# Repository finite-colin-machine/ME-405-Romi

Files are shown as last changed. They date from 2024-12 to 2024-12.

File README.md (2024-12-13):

# ME-405-Romi
## Project Overview and Results
Romi
**Figure 1:** Finished robot

This is the repository for the Cal Poly ME-405 term project by Colin Bentley and Jack Maxwell that required building and programming a line following differential drive robot. The robot follows a black line from the start box to the finish box and navigates around a wall obstacle along the way. After finishing, the robot drives back to start and prepares for another run. The robot features a line sensor, bump sensors, and a 9-DOF absolute orientation IMU to read heading and yaw. The robot can successfully navigate the course. The line following is accurate, even with challenging shapes like dashes and horizontal lines in the path, and the control system results in smooth driving.

[Watch Romi complete the course](https://cpslo-my.sharepoint.com/:v:/g/personal/cobentle_calpoly_edu/EcgrodB_KnZJpqk-TpCn7YkBvjt-W66TGioHFDayowuLnw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)

This project has room for future improvements. Currently, the wall navigation parameters have to be preprogrammed. Having the robot slowly bump around the wall similar to a Roomba could make this program more flexible for unknown obstacles while keeping the same bump sensors. The navigation from start to finish relies on the start box being directly behind the robot when it finishes the course. Adding calculations for the robot's postion while running through the course would allow it to drive back to start even if the start and finish boxes were moved. The program could run faster by using an analog line sensor or by configuring the digital sensor to work with interupts to prevent the program from waiting while reading the line. We noticed that battery voltage has a noticable impact on performance, and the control gains should be tuned to the specific voltage for best results.

## Hardware
The robot is built off a Romi chassis and controlled using a Nucleo L476RG running MicroPython. An additional circuit board called the Shoe of Brian attaches to the Nucleo. Information about the shoe and general support for the techniques used in this project can be found [here](https://github.com/spluttflob/ME405-Support).

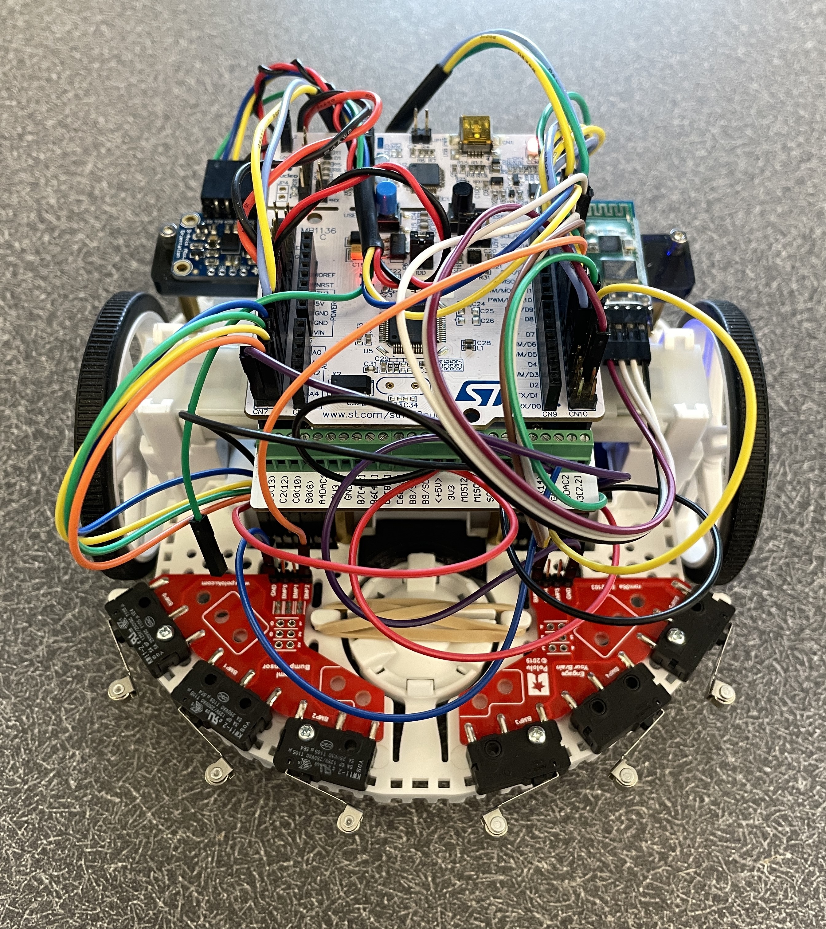
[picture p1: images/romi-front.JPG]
Romi Front


**Figure 2:** Romi front view with IMU and bluetooth module shown on the sides

The Nucleo attaches to standoffs and an acrylic mount as shown in this [model](https://cad.onshape.com/documents/b78783ff999bc8e6a9990234). The IMU and optional Bluetooth module are taped to the sides of the acrylic mount. The bump sensors screw directly to the front of the chassis, and the line sensor is taped to the line sensor mount which taped to the chassis.

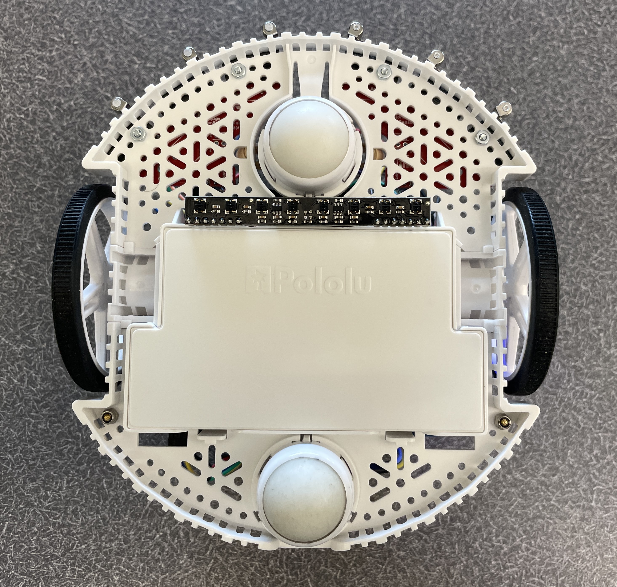
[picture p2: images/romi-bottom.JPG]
Romi Bottom


**Figure 3:** Romi bottom view with line sensor

Table 1 lists all of the parts besides the jumper wires used in this project.

**Table 1:** Complete BOM
| Part | Supplier  | P/N | Additional Info |
|---|---|---|---|
| Microcontroller | Nucleo | L476RG | |
| Shoe of Brian | Custom | N/A | [OSH Park](https://oshpark.com/shared_projects/e6X6OnYK) |
| Romi Chassis Kit | Pololu | 3509 | |
| Motor Driver and Power Distribution Board | Pololu | 3543 | |
| Line Sensor | Pololu | 3672 | |
| Right Bumper | Pololu | 3674 | |
| Left Bumper | Pololu | 3673 | |
| IMU | Adafruit  | 2472 | |
| Bluetooth Module | | HC-05  | Optional |
| Line Sensor Mount | Custom | N/A | See line-sensor-mount.STEP |
| Misc. mounts and fasteners | N/A | N/A | [Onshape](https://cad.onshape.com/documents/b78783ff999bc8e6a9990234) |

Figure 4 is a wiring diagram for the robot and, Table 2 lists the wire connections used.

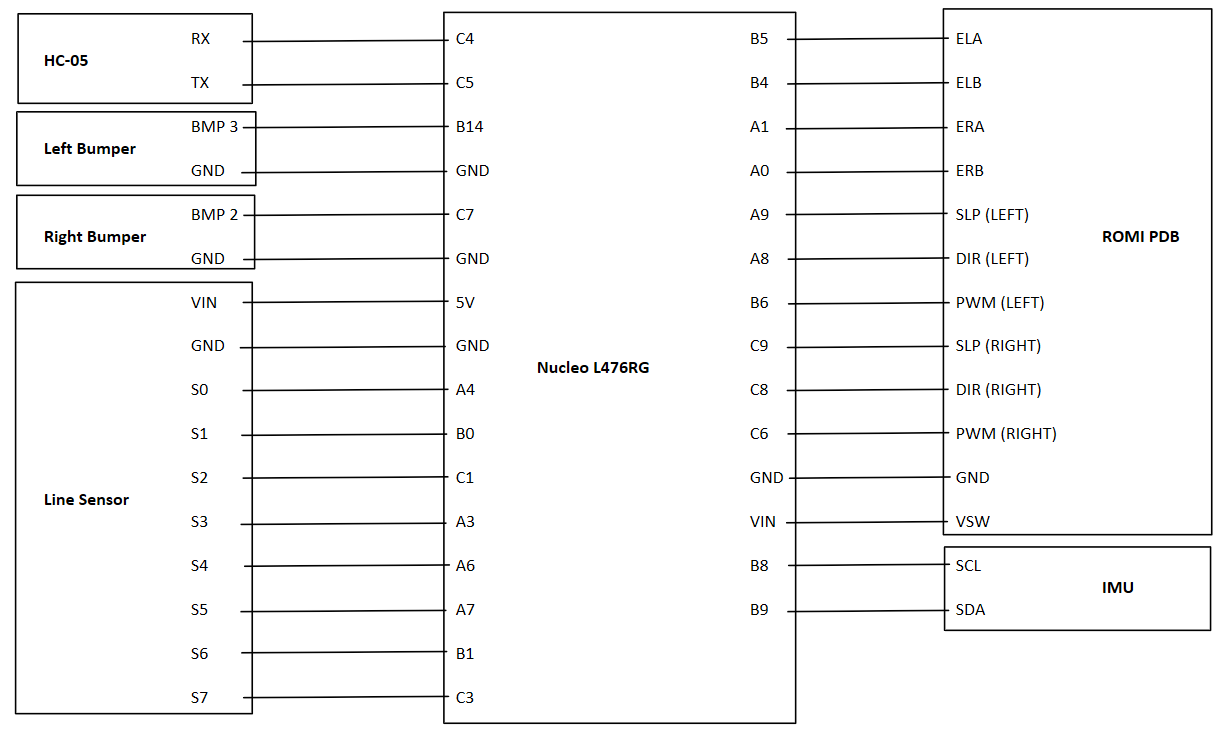
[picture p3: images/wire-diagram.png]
Wiring Diagram


**Figure 4:** Wiring diagram

**Table 2:** Wire connections
| Device/Function | Signal | Nucleo Pin | Device Pin |
|---|---|---|---|
| Left Encoder (Romi PDB)  | Enc Ch A | B5 (Tim 3) | ELA |
| | Enc Ch B | B4 (Tim 3) | ELB |
| Right Encoder (Romi PDB) | Enc Ch A | A1 (Tim 2) | ERA |
| | Enc Ch B | A0 (Tim 2) | ERB |
| Left Motor (Romi PDB) | Enable | A9 | SLP |
| | Direction | A8 | DIR |
| | Effort | B6 (Tim 4) | PWM |
| Right Motor (Romi PDB) | Enable | C9 | SLP |
| | Direction | C8 | DIR |
| | Effort | C6 (Tim 8) | PWM |
| Power (Romi PDB) | Ground | GND | GND |
| | Power | VIN | VSW |
| I2C | SCL | B8 | SCL |
| | SDA | B9 | SDA |
| HC-05 Bluetooth | RX | C4 | RX |
| | TX | C5 | TX |
| Left Bumper | BMP | B14 | BMP 3 |
| | GND | GND | GND |
| Right Bumper | BMP | C7 | BMP 2 |
| | GND | GND | GND |
| Line Sensor | Power | 5V | VIN |
| | GND | GND | GND |
| | Sensor 0 | A4 | S0 (R) |
| | Sensor 1 | B0 | S1 |
| | Sensor 2 | C1 | S2 |
| | Sensor 3 | A3 | S3 |
| | Sensor 4 | A6 | S4 |
| | Sensor 5 | A7 | S5 |
| | Sensor 6 | B1 | S6 |
| | Sensor 7 | C3 | S7 (L) |

Additionally, the IMU and Bluetooth Module are both wired to +5V and GND for their power supply.

## Code
The code folder contains all of the files that need to be stored on the Nucleo in order to run. This project uses MicroPython, which the nucleo needs to be preconfigured with before adding the other files. [main.py](code/main.py) contains the code to create and run the task structure, along with the initialization for all of the devices connected to the microcontroller. [encoder.py](code/encoder.py), [Romi_Motor.py](code/Romi_Motor.py), [BNO055.py](code/BNO055.py), and [line_sensor.py](code/line_sensor.py) contain classes for interacting with the encoders, motors, IMU, and line sensor repsectivly.

### Task Structure
Figure 5 contains the overall task diagram for the program that is run using preemptive multitasking. Scheduling and shares are handled by [cotask.py](code/cotask.py) and [task_share.py](code/task_share.py). We tuned the tasks to run as frequently as possible while still allowing all of the other tasks to run. The Planner has the highest priority but does not need to run often. Driving Mode has the next highest priority and needs to run often enough to get good line measurements; however, the line reading is time intensive and can easily overpower the other tasks if the period is too low. The control tasks have the lowest priority and run most often. This we can consistently measure good data and adjust the control setpoints, but it is okay if a higher priority task briefly blocks the control tasks from running.

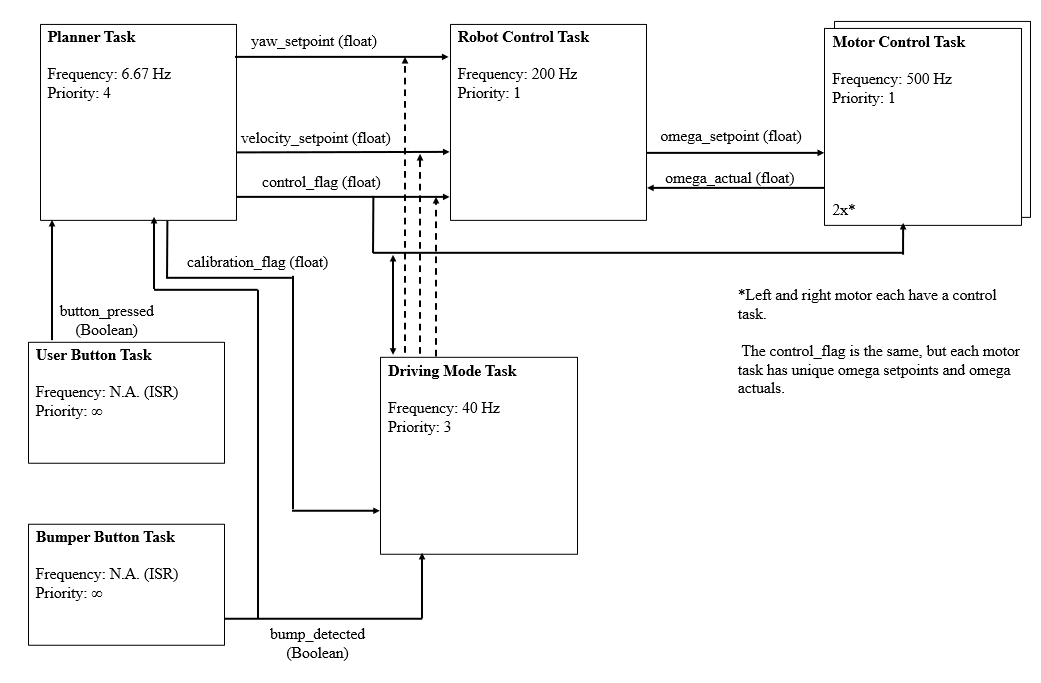
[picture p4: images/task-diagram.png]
Task Diagram


**Figure 5:** Overall task diagram

The Planner Task in our code is less complex than the other tasks, but is still crucial to the success of the program. In State 0, some system parameters are initialized, and on startup and when the code is reset from the PuTTY REPL, the task switches to State 2 for calibration. Upon successful calibration the task moves to State 1, where you are prompted to press the blue button to begin driving. Pressing the blue button will enable the system control loop and allow the robot to begin moving forward.

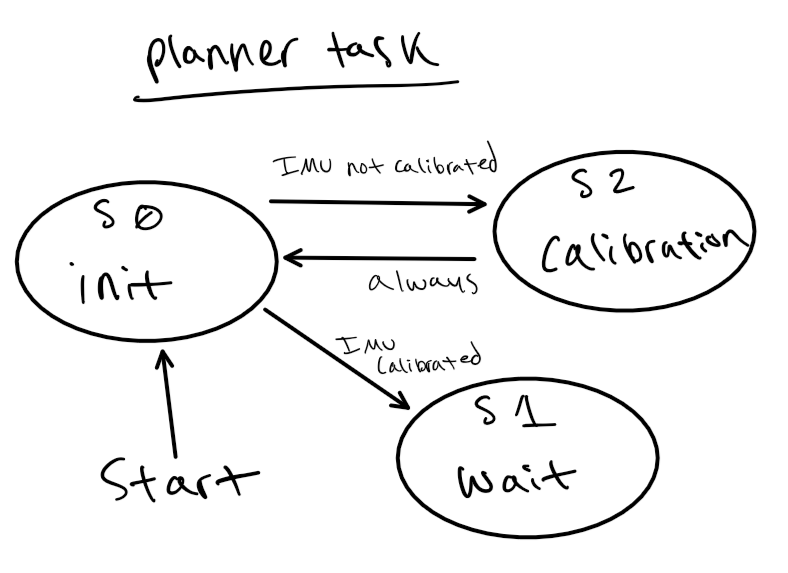
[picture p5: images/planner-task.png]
Planner Task


**Figure 6:** Planner Task State Transition Diagram

The robot control task is the outer loop of our system control, as seen in Figure 7. In State 1, this task takes in the translational velocity and yaw rate setpoints calculated by the driving mode task, as well as the actual wheel velocities calculated by the motor control task. Using the individual wheel velocities, this task calculates the actual translational velocity, and using the heading data from the IMU, calculates the actual yaw rate of Romi. PI Control (proportional and integral control) is performed on these values to calculate a velocity request and a yaw rate request, which are converted to a left and right wheel speed request, which are then sent to the individual wheel control tasks using shares. In State 0, the timer used to calculate the integral error for integral control is continuously reset to avoid integral error buildup while the control is off.

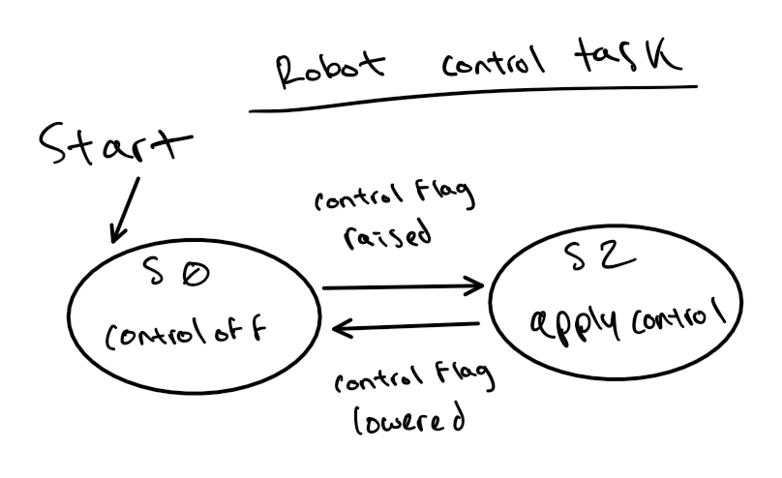
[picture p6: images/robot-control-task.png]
Robot Control Task


**Figure 7:** Robot Control Task State Transition Diagram

The motor control tasks act similarly to the overall robot control. They take in the setpoints for wheel velocity calculated by robot control and perform PI control on them to determine the duty cycle percentage that is sent to each motor. The actual velocities are sent to the robot control task when they are measured. Like the robot control, State 0 updates the encoder each pass-through to avoid integral error buildup.

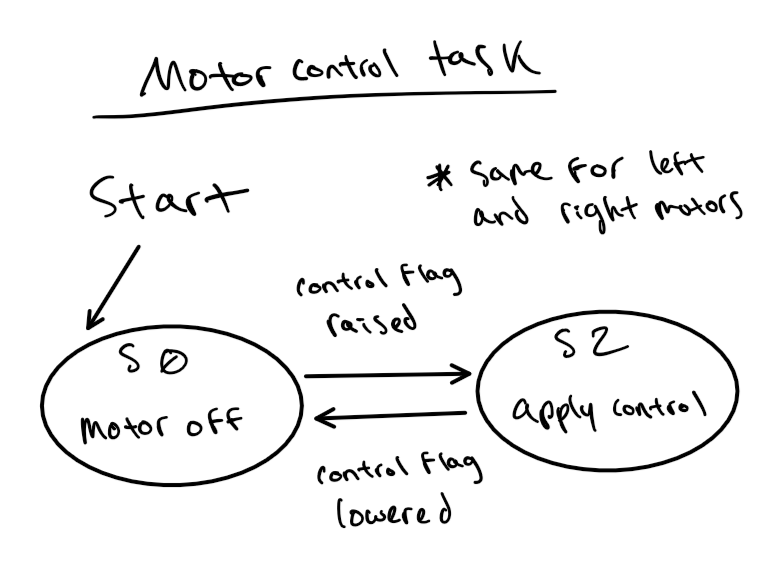
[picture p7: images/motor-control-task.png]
Motor Control Task


**Figure 8:** Motor Control Task State Transition Diagram

The driving mode task is our most complex task, as it is responsible for keeping the robot on the line and making it drive around the obstacle on the course. State 0 initializes some variables and flagsthat are used throughout the task, and when the system control flag is raised by the planner task, it moves to State 3, which instructs it to drive forward to leave the starting area. Once the robot has left the starting area, State 1 is entered, which is our main line-following state. This state reads the line sensor, and sends a yaw rate request to the system control based on the location of the line relative to the robot. When a bump is detected by the bump sensors mounted to the robot, the task enters State 2, where the robot is given a specific set of instructions to drive around the obstacle on the course, before returning to State 1 for line following.

When the robot enters the finishing area, the task enters State 4, where the robot drives to the center of the finishing area, and turns in place until its heading is 180 degrees past that of its initial heading. It then begins driving straight backwards and enters State 5. In State 5, the robot drives straight backward until it detects the starting area, where the task then enters State 6 to center itself in the box, and finally enters State 7 to turn the robot around and re-initialize the program to prepare for future runs.

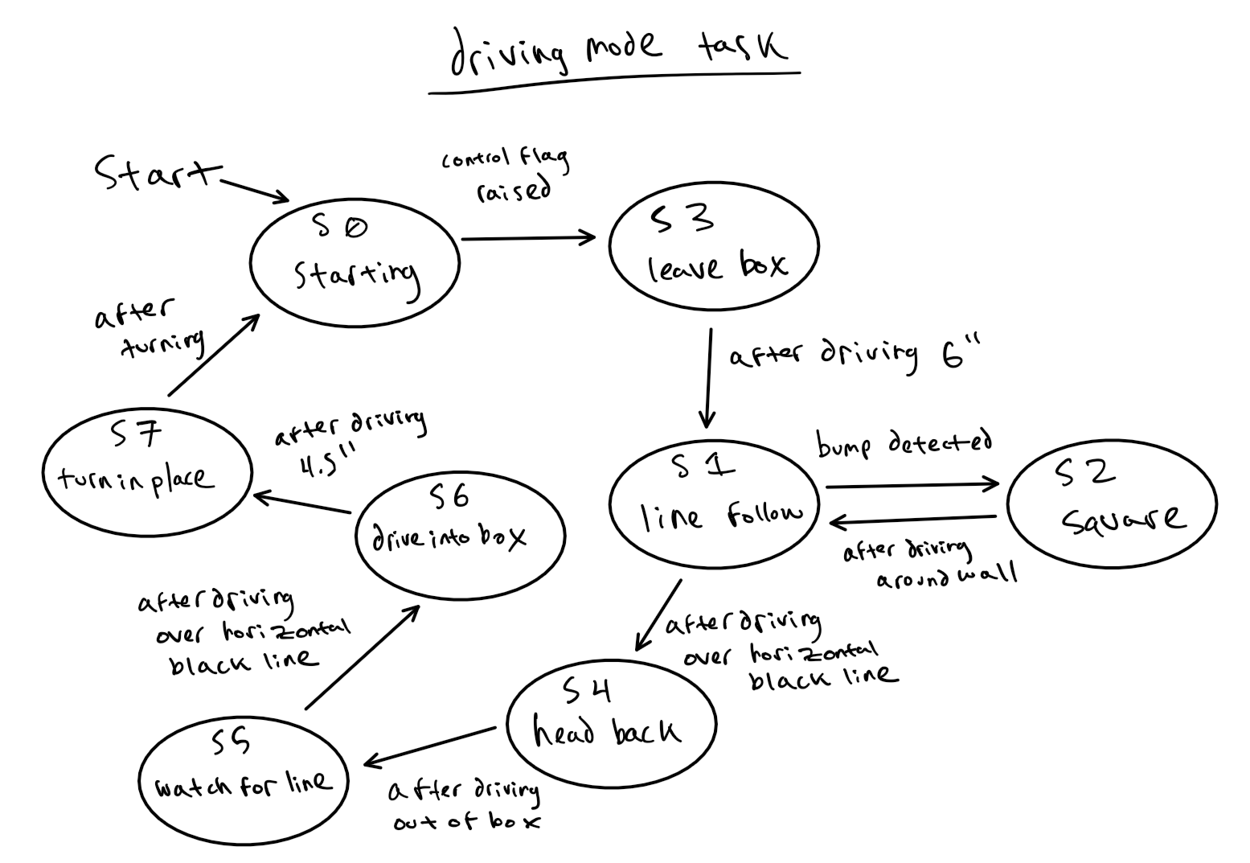
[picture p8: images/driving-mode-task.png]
Driving Mode Task


**Figure 9:** Driving Mode Task State Transition Diagram

### Control System
Figure 5 depicts the overall control system for the robot. We specify velocity and setpoints for the robot control loop either manually or using feedback from devices like the line sensor. . The robot control calculates the actual translational velocity using wheel speed measurements from the motor tasks and gathers yaw measurements from the IMU. Both are fed through PI control to become velocity and yaw requests. Omega setpoints are calculated from these requests using the robot parameters and sent to each of the motor control tasks. The motor control tasks perform PI control of the left and right wheel speeds using omega setpoints from the robot control and real omega measurements calculated from the encoders.

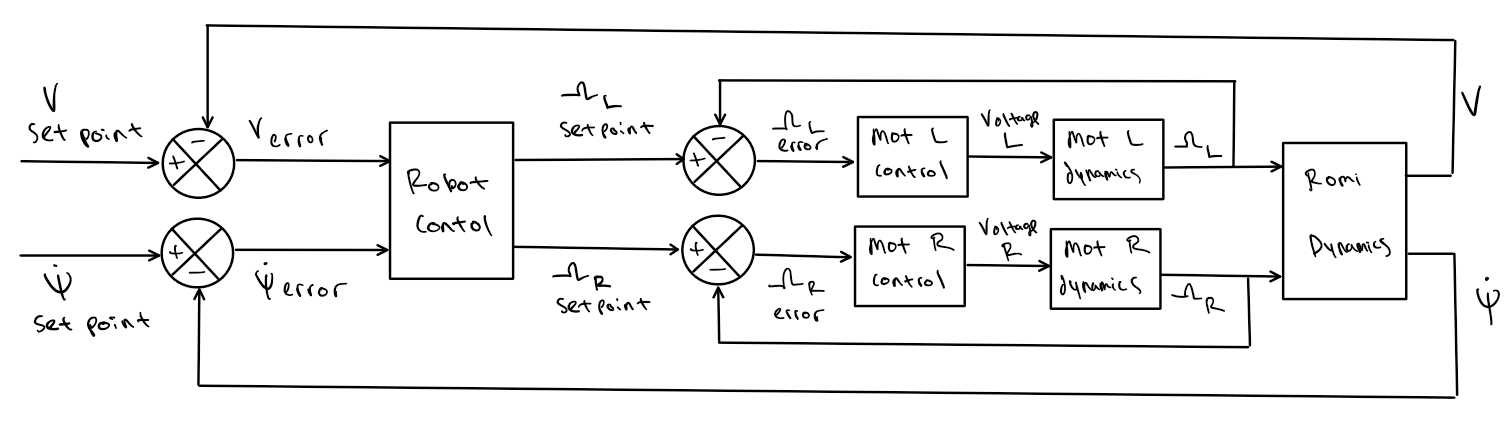
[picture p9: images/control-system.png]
Control System


**Figure 10:** Overall control system

## Supporting Calculations
Figures 11 and 12 show the calculations for translational velocity from the wheel speeds and the angular velocity setpoints from the velocity and yaw setpoints. These calculations are performed in the robot control task.

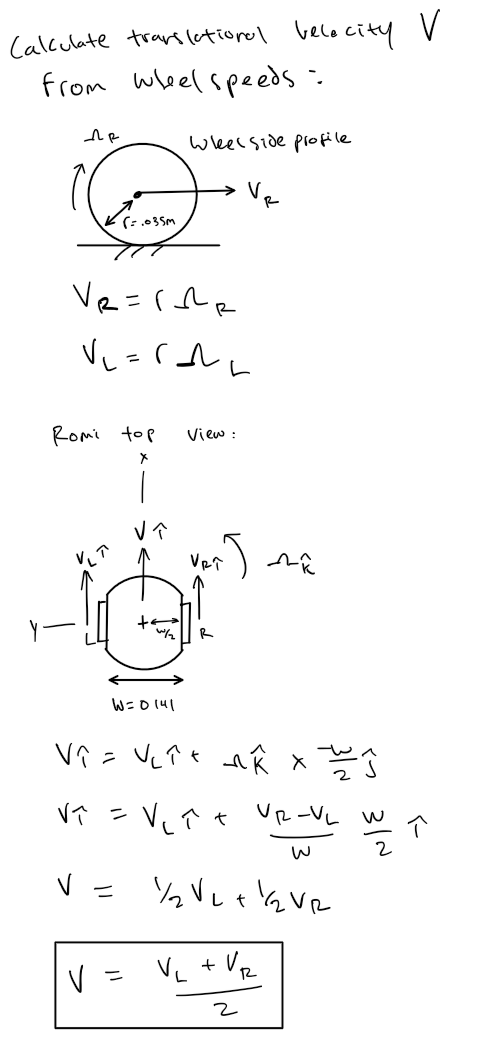
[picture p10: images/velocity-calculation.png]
Translational Velocity Calculation


**Figure 11:** Translational velocity calculation

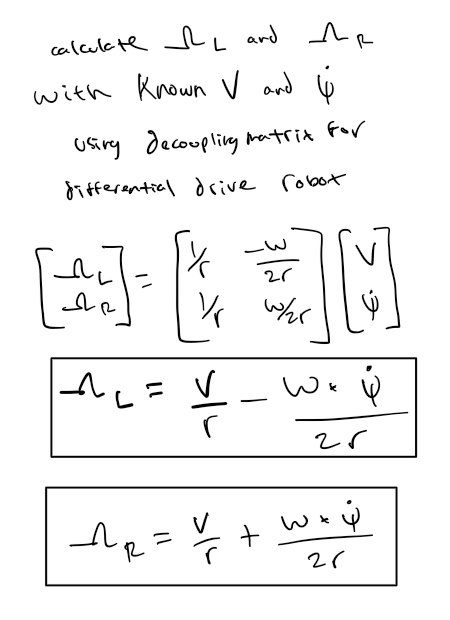
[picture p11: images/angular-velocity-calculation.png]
Angular Velocity Calculation


**Figure 12:** Angular velocity calculation

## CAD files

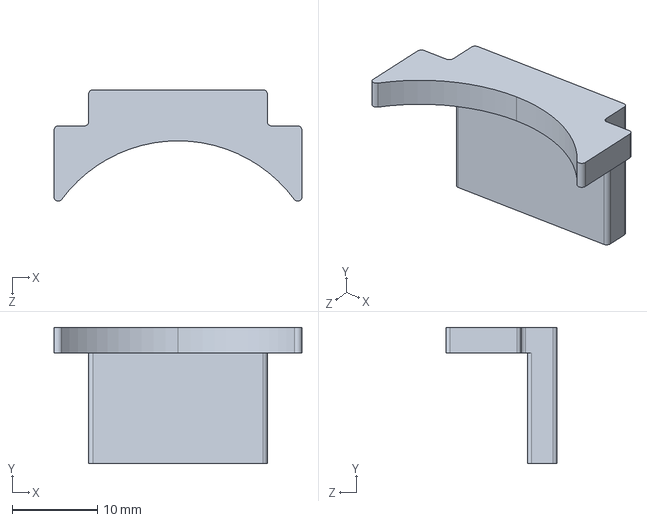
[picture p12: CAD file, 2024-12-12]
line-sensor-mount.STEP
29.2 x 16.0 x 13.1 mm

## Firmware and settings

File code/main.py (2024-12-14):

"""!
@file main.py 
@author Colin Bentley and Jack Maxwell
@date 12/13/2024

This program is used to make a Romi robot follow a line-based obstacle course.
This program is part of assignment Term Project 0x02 - Romi Time-Trials for ME 405.

Users place Romi inside the starting area and press the blue botton to start, and
thr robot autonomously guides itself through the course to the finsih line, and returns
to the startimng area.

Romi accomplishes this by taking readings with a line sensor, which are converted to 
yaw-rate changes for the control scheme to follow. Additionally, there is a bump sensor
mounted to the robot that when presses, puts the robot into a pre-set path around the 
obstacle before resuming line-following.

The standard control scheme uses a robot control task that takes in yaw rate and velocity
information, and feeds wheel speed setpoints to the motor control tasks.
"""

# Import modules
from pyb import Pin, Timer, UART, repl_uart, ExtInt
import gc
import machine
import cotask
import task_share
from encoder import encoder
from Romi_Motor import Romi_Motor             
from BNO055 import BNO055
from time import ticks_us, ticks_diff, sleep_ms
from math import pi
from line_sensor import line_sensor

# Blue user button function
def user_button_toggle(pressed):
    global user_button_pressed
    user_button_pressed = True

# Bump sensor function
def bump_toggle(pressed):
    global bump_detected
    bump_detected = True
    print('Hey! Who put that there?')
    # The bump sensors have a small amount of signal bouncing - this
    # is handled by not resetting the bump_detected flag until the
    # end of the pre-coded sequence.

# Create generator functions acting as tasks containing FSMs
def planner(shares):
    """!
    Task which handles the IMU calibratrion and waits for the blue button to be pressed.
    @param shares A tuple of a share and queue from which this task gets data
    """
    global user_button_pressed, bump_detected # list global variables
    
    # get references to the shares and queues which have been passed to this task
    my_velocity_setpoint, my_yaw_setpoint, my_control_flag, my_calibration_flag = shares
    
    state = 0                  # initialize state
    calibrated = False         # initialize calibration
    my_calibration_flag.put(0) # initialize calibration flag

    while True:
        if (state == 0):                        # init state
            V = .10                             # user input robot translational velocity [m/s]
            
            # # # TO BYPASS CALIBRATION CHECK
            # calibrated = True
            # print('bypassing calibration')
            
            if calibrated == False:
                state = 2   # set calibration state
            else:
                print('Press blue button to begin driving')
                state = 1   # set wait state
            yield(state)  
            
        elif (state == 1):  # wait and search for bump state state
            if user_button_pressed == True:
                user_button_pressed = False    # if so, reset the user button flag
                my_control_flag.put(1)         # raise control flag       
                my_velocity_setpoint.put(V)    # set velocity for robot control task
                my_yaw_setpoint.put(0)         # set yaw rate for robot control task
            yield(state)
        
        elif (state == 2):                           # calibration state
            
            file_known = False                       # initialize flag
            calibrated = False                       # initialize calibration status
        
            try:                                     # try to open calibration file
                with open('calibration.bin', 'r'):
                    file_known = True                # set flag
            except OSError:                          # if there is no calibration file
                print('Perform manual calibration')  # notify user
        
            if file_known:
                try:
                    IMU.set_offsets()                # calibrate using file data
                    calibrated = True                # set calibrated
                except OSError:                      # if there is an error using the file
                    raise OSError('''Error accessing calibration.bin. Remove calibration.bin from the nucleo and restart program to perform manual calibration''')
                                  
        
            if not calibrated:                       # if still not calibrated
                IMU.read_cal_status()                # read calibration status
                print(f"{IMU.mag_cal_status} {IMU.acc_cal_status} {IMU.gyr_cal_status} {IMU.sys_cal_status}")
                if (IMU.mag_cal_status == 3
                    and IMU.acc_cal_status == 3
                    and IMU.gyr_cal_status == 3
                    and IMU.sys_cal_status == 3):    # if all calibrated
                    calibrated = True                # set calibrated
                    print('IMU Calibrated')          # notify user
                    my_calibration_flag.put(1)
                    
            state = 0                                # set init state
            yield(state)
        
        else: # if state isnt found
            raise ValueError('Invalid state')

def robot_control(shares):
    """!
    Controller task which calculates omega setpoints for the motors using translationa velocity and yaw data.
    Comment out this task and follow other instructions in the code to bypass the robot control.
    @param shares A tuple of a share and queue from which this task gets data
    """
    global w, r # list global variables
    
    # get references to the shares and queues which have been passed to this task
    my_velocity_setpoint, my_yaw_setpoint, my_control_flag, my_omega_L_setpoint, my_omega_R_setpoint, my_omega_L_actual, my_omega_R_actual = shares
    
    V_err = 0       # zero error
    yaw_err = 0     # zero error
    V_err_sum = 0   # zero error sum
    yaw_err_sum = 0 # zero error sum
    
    state = 0       # initialize state
    
    # set proportional and integral gains for translational velocity and yaw rate
    Kp_V = .8
    Kp_yaw = .7
    Ki_V = .87
    Ki_yaw = .95
    
    while True:
        control_on = my_control_flag.get() # get control flag
        
        if state == 0:            # State 0: Robot Control off
            time_old = ticks_us() # continuously update old time while off
            if control_on == 0:   # set to control state if flag raised
                pass
            else:
                state = 1         # set control state
            yield(state)                   
            
        elif state == 1: # State 1: Apply control     

            # get values from shares
            V_ref = my_velocity_setpoint.get()
            yaw_ref = my_yaw_setpoint.get()
            omega_L_act = my_omega_L_actual.get()
            omega_R_act = my_omega_R_actual.get()
            
            # perform time calculations
            time_new = ticks_us()                         # update time
            dt = ticks_diff(time_new, time_old)/1_000_000 # calculate time difference in seconds
            time_old = time_new                           # reset the old time for next pass 
        
            # calculate actual translational velocity based on current wheel velocity
            V_act = (r/2)*(omega_L_act + omega_R_act)     
            
            # read actual yaw rate from IMU
            IMU.read_gyr()              
            yaw_act = IMU.gyr_z*0.01745 # [rad/s] convert yaw rate from deg/s to rad/s
      
            # calculate errors
            V_err = V_ref - V_act
            yaw_err = yaw_ref - yaw_act
            
            # calculate error sums
            V_err_sum += V_err*dt
            yaw_err_sum += yaw_err*dt
            
            # calculate robot requests by applying proportional and integral control
            V_request = Kp_V*V_err + Ki_V*V_err_sum
            yaw_request = Kp_yaw*yaw_err + Ki_yaw*yaw_err_sum
            
            # calculate wheel velocity requests from robot requests
            omega_L_request = (V_request/r) - (w*yaw_request/(2*r))
            omega_R_request = (V_request/r) + (w*yaw_request/(2*r))
            
            # add wheel velocities to shares
            my_omega_L_setpoint.put(omega_L_request)
            my_omega_R_setpoint.put(omega_R_request)
            
            if control_on == 1: # set to control off state if flag lowered
                pass
            else:
                V_err = 0       # zero velocity error
                yaw_err = 0     # zero yaw rate error
                V_err_sum = 0   # zero velocity error sum
                yaw_err_sum = 0 # zero yaw rate error sum

                state = 0       # set off state
            yield(state)
           
        else:                   # if state isnt found
            raise ValueError('Invalid state')

def motor_L_control(shares):
    """!
    Task which controls the velocity of the left motor by applying proportional and integral control to the velocity error
    @param shares is a tuple of a share and queue from which this task gets data
    """
    # get references to the shares and queues which have been passed to this task
    my_omega_L_setpoint, my_omega_L_actual, my_control_flag = shares
    
    state = 0       # initialize state
    mot_L.disable() # disable motor
    Kp = 7          # set proportional gain
    Ki = 8          # set integral gain
    err_sum = 0     # initialize error sum
    
    while True:
        motor_on = my_control_flag.get() # get control flag from shares
        
        if state == 0:        # State 0: Motor Off
        
            enc_L.update()    # continuously update encoder while off
            if motor_on == 0: # set to control state if flag raised
                pass
            else:
                mot_L.set_duty(0) # clear duty cycle
                mot_L.enable()    # enable motor
                state = 1         # set control state
            yield(state)
        
        elif state == 1: # State 1: Apply Motor Control
            
        # get wheel velocity from shares
            Omega_L_ref = my_omega_L_setpoint.get()
            
            # update encoder and get dt
            enc_L.update()
            dt = enc_L.get_dt()/1_000_000 # [s]
            
            # calculate omega actual
            Omega_act = enc_L.get_speed()*-4363 # [rad/s], multiplier is speed count/us * 10^6 us/s * 1/1440 rev/count * 2pi rad/rev
            my_omega_L_actual.put(Omega_act)    # add to wheel velocity share

            # Apply motor control
            err = Omega_L_ref - Omega_act # calculate error
            err_sum += err*dt             # calculate error sum
            L = Kp*err + Ki*err_sum       # calculate duty cycle
            mot_L.set_duty(L)             # set duty cycle
            
            if motor_on == 1:     # set to off state if flag lowered
                pass
            else:
                mot_L.set_duty(0) # clear duty cycle
                mot_L.disable()   # disable motor
                err_sum = 0       # clear error sum
                state = 0         # set off state
            yield(state)

def motor_R_control(shares):
    """!
    Task which controls the velocity of the right motor by applying proportional and integral control to the velocity error
    @param shares is a tuple of a share and queue from which this task gets data
    """
    # get references to the shares and queues which have been passed to this task
    my_omega_R_setpoint, my_omega_R_actual, my_control_flag = shares
    
    state = 0       # initialize state
    mot_R.disable() # disable motor
    Kp = 7          # set proportional gain
    Ki = 8          # set integral gain
    err_sum = 0     # initialize error sum
    
    while True:
        motor_on = my_control_flag.get() # get control flag from shares
        
        if state == 0:        # State 0: Motor Off
            
            enc_R.update()    # continuously update encoder while off
            if motor_on == 0: # set to control state if flag raised
                pass
            else:
                mot_R.set_duty(0) # clear duty cycle
                mot_R.enable()    # enable motor
                state = 1         # set control state
            yield(state)
        
        elif state == 1: # State 1: Apply Motor Control
            
            # get wheel velocity from shares
            Omega_R_ref = my_omega_R_setpoint.get()
            
            # update encoder and get dt
            enc_R.update()
            dt = enc_R.get_dt()/1_000_000 # [s]
            
            # calculate omega actual
            Omega_act = enc_R.get_speed()*-4363 # [rad/s], multiplier is speed count/us * 10^6 us/s * 1/1440 rev/count * 2pi rad/rev
            my_omega_R_actual.put(Omega_act)    # add to share

            # Apply motor control
            err = Omega_R_ref - Omega_act # calculate error
            err_sum += err*dt             # calculate error sum
            L = Kp*err + Ki*err_sum       # calculate duty cycle
            mot_R.set_duty(L)             # set duty cycle
            
            if motor_on == 1:     # set to off state if flag lowered
                pass
            else:
                mot_R.set_duty(0) # clear duty cycle
                mot_R.disable()   # disable motor
                err_sum = 0       # clear error sum
                state = 0         # set off state
            yield(state)
            
def driving_mode(shares):
    """!
    Task which handles the line following and obstacle avoidance behavior of the robot. The robot
    follows the line until a bump is detected, drives around the obstacle, and returns to line
    following until reaching the finish line, where the robot then returns to the start.
    @param shares is a tuple of a share and queue from which this task gets data 
    """
    global bump_detected # list global variables
    
    # get references to the shares and queues which have been passed to this task
    my_velocity_setpoint, my_yaw_setpoint, my_control_flag, my_calibration_flag = shares
    
    V = .10                             # user input robot translational velocity [m/s]
    w = .141                            # robot track width [m]
    r = .035                            # robot wheel radius [m]
    
    drive_3 = 1440*3*.0254/(2*pi*r)     # distance for robot to drive 3 inches [encoder counts]
    turn_90 = 1440*w/(8*r)              # distance for robot to turn 90 degrees in place [encoder counts]
    
    # init variables
    after_wall = False  # flag that is raised once the obstacle has been cleared
    state = 0
    
    while True:
        if state == 0:                                 # starting state
            control_on = my_control_flag.get()         # get control flag
            calibrated = my_calibration_flag.get()     # get calibration flag
            if calibrated == 0:                        # ignore bump detection before calibration
                bump_detected = False
            if control_on == 1:                        # set to control state if flag raised
                IMU.read_euler()                       # read the IMU
                starting_heading = IMU.euler_heading   # retrieve the robots heading to allow it to return to the start
                enc_R.zero()                           # clear encoder position
                state = 3                              # set leave box
            yield(state)                   
        
        elif state == 1:                                        # line follow state
            if bump_detected:                                   # if there is a bump
                my_control_flag.put(0)                          # turn off motors
                enc_R.zero()                                    # clear encoder
                section_complete = False                        # Initialize square section completion flag
                square_idx = 1                                  # Init square index
                state = 2                                       # set square driving state
            elif after_wall == True and qtr.full_black == True: # if robot crosses black line after bumping wall, it's at the finish line
                my_velocity_setpoint.put(V)                     # set velocity
                my_yaw_setpoint.put(0)                          # set yaw
                enc_R.zero()                                    # clear encoder
                after_wall = False                              # reset flag for future runs
                return_idx = 1                                  # initialize return sequence index
                state = 4                                       # set turn around state
            else:                                               # otherwise
                yaw = qtr.read_line()/1500                      # read line and scale measurement
                if qtr.full_black:                              # if the robot senses a prependicular line
                    my_yaw_setpoint.put(0)                      # set yaw to zero to minimize "twitching"
                else:
                    my_yaw_setpoint.put(yaw)                    # Set yaw based on line reading
            yield(state)   
            
        elif state == 2:                          # drive in square state
            enc_R.update()                        # Update encoder position
            position = abs(enc_R.get_position())  # Get position magnitude
            
            if square_idx == 1 and not section_complete:  # Step 1: Back up
                my_velocity_setpoint.put(-V)  # Set reverse velocity
                my_yaw_setpoint.put(0)        # No yaw change
                my_control_flag.put(1)        # Start movement
                if position > drive_3 / 2:    # Condition to finish backing up
                    my_control_flag.put(0)    # turn off control so the robot stops at each step
                    square_idx += 1           # increase the square path index
                    enc_R.zero()              # zero encoders
                    section_complete = True   # raise section complete flag so the next square step isn't entered immediately
            
            elif square_idx in [2, 4] and not section_complete:  # Steps 2 and 4: Turn 90 degrees
                turn_speed = -pi/2 if square_idx == 2 else pi/2  # turn left for state 2, right for state 4
                my_velocity_setpoint.put(0)      # No forward motion
                my_yaw_setpoint.put(turn_speed)  # Set yaw rate
                my_control_flag.put(1)           # Start turn
                if position > turn_90:           # Condition to finish turn
                    my_control_flag.put(0)
                    square_idx += 1
                    enc_R.zero()
                    section_complete = True
            
            elif square_idx == 3 and not section_complete:  # Steps 3: Drive forward short distance
                my_velocity_setpoint.put(V)  # Forward velocity
                my_yaw_setpoint.put(0)       # No yaw change
                my_control_flag.put(1)       # Start forward motion
                if position > drive_3 * 3:   # Condition to finish drive
                    my_control_flag.put(0)
                    square_idx += 1
                    enc_R.zero()
                    section_complete = True
            
            elif square_idx == 5 and not section_complete:  # Step 5: Drive forward longer distance
                my_velocity_setpoint.put(V)  # Forward velocity
                my_yaw_setpoint.put(0)       # No yaw change
                my_control_flag.put(1)       # Start forward motion
                if position > drive_3 * 6:   # Condition to finish drive
                    my_control_flag.put(0)
                    square_idx += 1
                    enc_R.zero()
                    section_complete = True
                    
            elif square_idx == 6 and not section_complete:  # Step 6: Turn slightly less than 90 degrees
                my_velocity_setpoint.put(0)  # No forward motion
                my_yaw_setpoint.put(pi/2)    # Set yaw rate
                my_control_flag.put(1)       # Start turn
                if position > turn_90 * .65: # Condition to finish turn
                    my_control_flag.put(0)
                    square_idx += 1
                    enc_R.zero()
                    section_complete = True
                    
            elif square_idx == 7 and not section_complete:  # Step 7: Drive forward until the line has been reached
                my_velocity_setpoint.put(V)  # Forward velocity
                my_yaw_setpoint.put(0)       # No yaw change
                my_control_flag.put(1)       # Start forward motion
                if position > drive_3 * 4:   # Condition to finish drive
                    enc_R.zero()
                    square_idx = 0          # Reset for future operations
                    bump_detected = False   # reset the bump detection flag
                    after_wall = True       # raise obstacle cleared flag
                    state = 1               # return to line following
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

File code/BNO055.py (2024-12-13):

"""!
@file BNO055.py
@brief A MicroPython driver for the BNO055 IMU.
@details This program provides an interface for the BNO055 IMU sensor using I2C communication. 
         It supports operations such as setting modes, retrieving calibration data, and reading 
         orientation and angular velocity data. The implementation is inspired by existing drivers 
         like the MicroPython-BNO055 driver by Peter Hinch and the Adafruit CircuitPython driver by Radomir Dopieralski.
@author Colin Bentley and Jack Maxwell
@date 11/19/2024
"""

# import modules
import machine
import time
import struct

# BNO055 register addresses
dev_addr = 0x28              # Default I2C address for the BNO055
euler_addr = 0x1A            # Register address for Euler angles
gyr_addr = 0x14              # Register address for gyroscope data
cal_status_addr = 0x35       # Register address for calibration status
mode_addr = 0x3D             # Register address for operation mode
acc_offset_addr = 0x55       # Register address for accelerometer offsets
mag_offset_addr = 0x5C       # Register address for magnetometer offsets
gyr_offset_addr = 0x62       # Register address for gyroscope offsets
unit_addr = 0x3B             # Register address for unit selection

# BNO055 mode numbers
imu_modes = {
    'imuplus': 0x08,          # IMU mode without magnetometer
    'compass': 0x09,          # Compass mode
    'm4g': 0x0A,              # Magnetometer with accelerometer mode
    'ndof_fmc_off': 0x0B,     # NDOF mode without fast magnetometer calibration
    'ndof': 0x0C,             # Full NDOF mode
    'config': 0}              # Configuration mode


class BNO055:
    '''!@brief A MicroPython driver for the BNO055 IMU.
    @details This class provides methods for configuring the BNO055 IMU, retrieving
             calibration data, and reading sensor measurements such as Euler angles
             and angular velocity.
    '''

    def __init__(self, i2c):
        '''!@brief Initializes the BNO055 driver with a given I2C interface.
        @details Sets the initial configuration and prepares the IMU for operation.
        @param i2c A pre-configured I2C object for communicating with the IMU.
        '''
        self.imu = i2c
        self.mode_number = imu_modes['config']  # Start in configuration mode

    def set_opr_mode(self, mode):
        '''!@brief Sets the operating mode of the IMU.
        @details Changes the mode of the BNO055 IMU to one of the supported modes, such as NDOF or IMUPLUS.
        @param mode The name of the mode to set (e.g., 'ndof', 'config').
        '''
        self.mode_name = mode
        self.mode_number = imu_modes[mode]     # Get mode number from the dictionary
        buf = bytearray([self.mode_number])    # Create a buffer with the mode number
        self.imu.writeto_mem(dev_addr, mode_addr, buf)  # Write mode to the operation mode register

    def read_cal_status(self):
        '''!@brief Reads the calibration status of the IMU.
        @details Retrieves the calibration levels of the system, gyroscope, accelerometer, and magnetometer.
        '''
        buf = bytearray(1)                     # Initialize a single-byte buffer
        self.imu.readfrom_mem_into(dev_addr, cal_status_addr, buf)  # Read the calibration status byte
        cal_status = buf[0]
        # Parse the status byte to retrieve individual calibration levels
        self.sys_cal_status = (cal_status >> 6) & 0x03
        self.gyr_cal_status = (cal_status >> 4) & 0x03
        self.acc_cal_status = (cal_status >> 2) & 0x03
        self.mag_cal_status = cal_status & 0x03

    def read_cal_coef(self):
        '''!@brief Reads the calibration coefficients from the IMU.
        @details Retrieves calibration offsets and saves them to a binary file.
        '''
        last_mode = self.mode_name              # Save the current mode
        self.set_opr_mode('config')             # Switch to configuration mode
        buf = bytearray(22)                     # Initialize a buffer for calibration data
        self.imu.readfrom_mem_into(dev_addr, acc_offset_addr, buf)  # Read offsets into buffer
        with open('calibration.bin', 'wb') as file:
            file.write(buf)                     # Save calibration data to a binary file
        self.set_opr_mode(last_mode)            # Restore the previous mode

    def set_offsets(self):
        '''!@brief Writes calibration coefficients to the IMU.
        @details Loads calibration offsets from a binary file and writes them to the IMU.
        '''
        last_mode = self.mode_name              # Save the current mode
        self.set_opr_mode('config')             # Switch to configuration mode
        with open('calibration.bin', 'rb') as file:
            buf = bytearray(file.read())        # Read calibration data from the file
        self.imu.writeto_mem(dev_addr, acc_offset_addr, buf)  # Write offsets to the IMU
        self.set_opr_mode(last_mode)            # Restore the previous mode

    def read_euler(self):
        '''!@brief Reads Euler angles from the IMU.
        @details Retrieves the heading, roll, and pitch angles for orientation feedback.
        '''
        buf = bytearray(6)                      # Initialize a buffer for Euler angle data
        self.imu.readfrom_mem_into(dev_addr, euler_addr, buf)  # Read data into the buffer
        # Unpack the data into individual angles
        self.euler_heading, self.euler_roll, self.euler_pitch = struct.unpack('<hhh', buf)
        self.euler_heading /= 16               # Convert heading to degrees

    def read_gyr(self):
        '''!@brief Reads angular velocity from the IMU.
        @details Retrieves the angular velocity in x, y, and z axes.
        '''
        buf = bytearray(6)                      # Initialize a buffer for gyroscope data
        self.imu.readfrom_mem_into(dev_addr, gyr_addr, buf)  # Read data into the buffer
        # Unpack the data into individual axes
        self.gyr_x, self.gyr_y, self.gyr_z = struct.unpack('<hhh', buf)
        self.gyr_z /= 16                        # Convert yaw rate to degrees/second

if __name__ == '__main__':
    i2c1 = machine.I2C(1)  # Configure I2C on pins B8 (SCL) and B9 (SDA)
    IMU = BNO055(i2c1)     # Initialize the IMU
    IMU.set_opr_mode('ndof')  # Set the IMU to NDOF mode

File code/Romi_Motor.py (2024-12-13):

"""!
@file Romi_Motor.py
@brief A driver class for controlling DC motors on the Romi robot.
@details This file contains the implementation of a motor driver class for the 
         DRV8838 motor driver used in the Pololu Romi robot. The class allows for
         precise control of the motor's speed and direction via PWM signals and 
         provides methods to enable and disable the motor driver.

Classes:
    - Romi_Motor: A class to control a single DC motor using the DRV8838 driver.

@author Colin Bentley and Jack Maxwell
@date 11/19/2024
"""

from pyb import Pin, Timer

class Romi_Motor:
    '''!@brief A driver class for the DRV8838 Motors on Romi.
    @details Objects of this class can be used to control a DRV8838 DC motor
    on the Romi robot by setting the PWM duty cycle, direction, and enabling
    or disabling the motor driver. This driver is designed for the Romi robot
    from Pololu, which uses the DRV8838 motor driver.
    '''

    def __init__(self, PWM_tim, PWM_pin, DIR_pin, EN_pin):
        '''!@brief Initializes and returns an object associated with a DC motor.
        @details This constructor configures the PWM channel, direction pin, and
        enable pin needed to control the motor. It sets default values to ensure
        the motor starts in a known state.
        @param PWM_tim The Timer object used for generating the PWM signal.
        @param PWM_pin The Pin object connected to the PWM input of the motor driver.
        @param DIR_pin The Pin object connected to the direction control pin.
        @param EN_pin The Pin object connected to the enable (not sleep) pin of the motor driver.
        '''
        self.CH = PWM_tim.channel(1, mode=Timer.PWM, pin=PWM_pin, pulse_width_percent=0)  # Configure PWM on CH1
        self.DIR = Pin(DIR_pin, mode=Pin.OUT_PP)  # Configure direction pin
        self.DIR.high()  # Set direction pin high (default to forward)
        self.EN = Pin(EN_pin, mode=Pin.OUT_PP)  # Configure enable pin
        self.EN.low()  # Turn off the enable pin (default to disabled)

    def set_duty(self, duty):
        '''!@brief Sets the PWM duty cycle for the DC motor.
        @details This method adjusts the motor's duty cycle to control its
        speed and direction. Positive values make the motor turn in one direction
        (e.g., forward), while negative values reverse the direction.
        @param duty A signed integer or float specifying the duty cycle
                    of the PWM signal as a percentage (-100 to 100).
        '''
        # Set direction based on duty sign
        if duty >= 0:  # For positive inputs
            self.DIR.low()  # Set direction for forward rotation
        else:  # For negative inputs
            self.DIR.high()  # Set direction for reverse rotation
        
        # Set the PWM duty cycle (absolute value of input)
        self.CH.pulse_width_percent(abs(duty))

    def enable(self):
        '''!@brief Enables the motor driver.
        @details This method sets the enable (not sleep) pin of the motor driver
        high to allow the motor to operate. The motor will respond to PWM and
        direction signals when enabled.
        '''
        self.EN.high()  # Enable the motor driver

    def disable(self):
        '''!@brief Disables the motor driver.
        @details This method sets the enable (not sleep) pin of the motor driver
        low to disable the motor. The motor will not respond to any PWM or
        direction signals while disabled.
        '''
        self.EN.low()  # Disable the motor driver
